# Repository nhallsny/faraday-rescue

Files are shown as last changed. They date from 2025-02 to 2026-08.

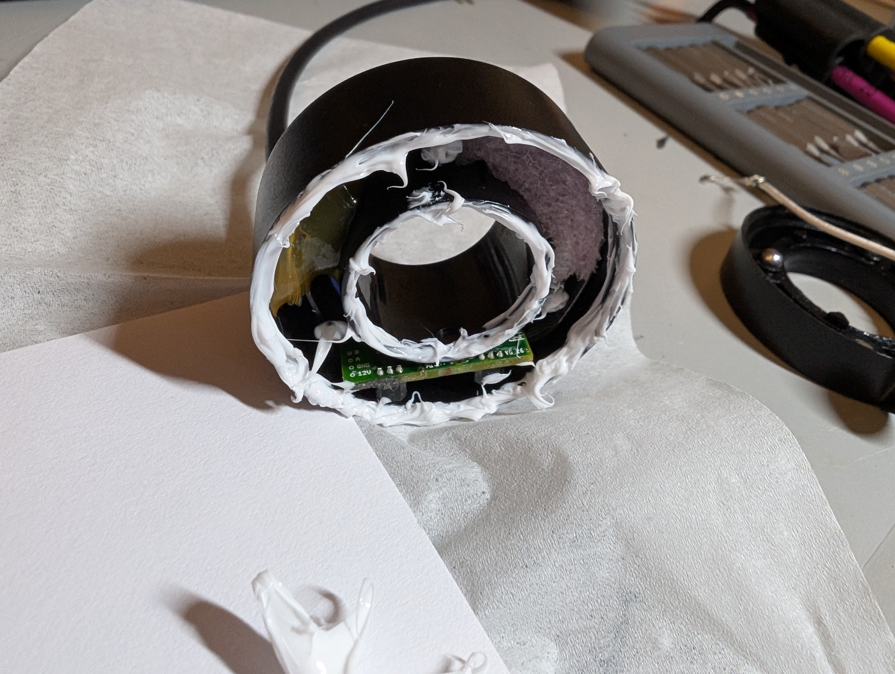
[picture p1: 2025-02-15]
reference/teardowns/mode_selector/PXL_20250124_061346121 - Copy.jpg

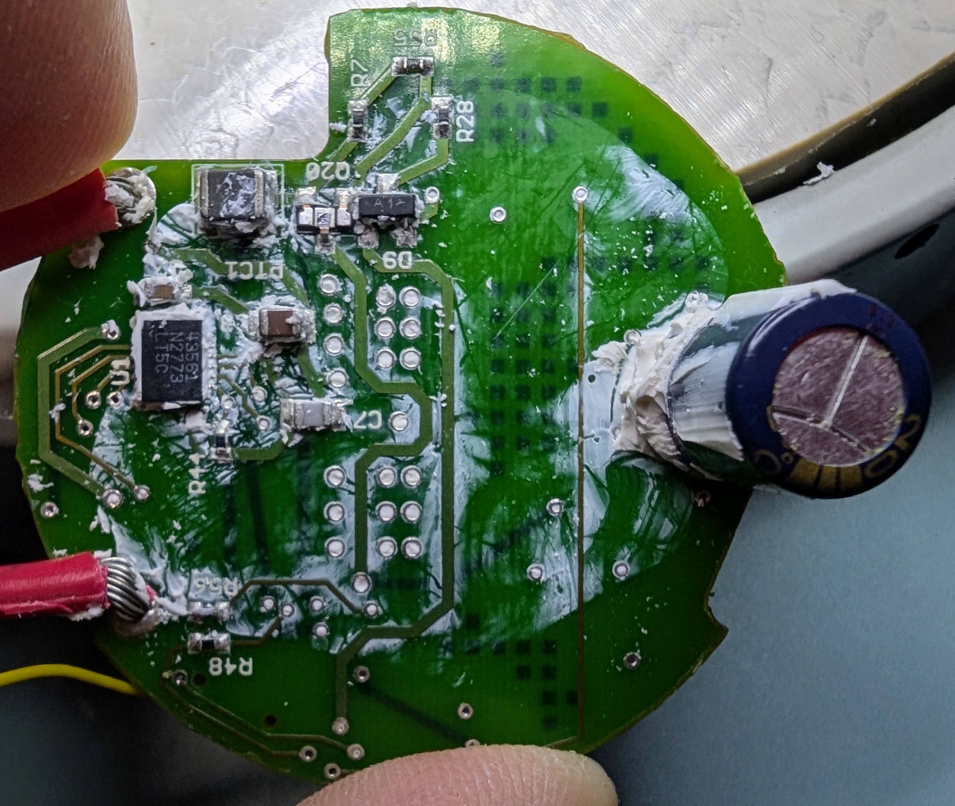
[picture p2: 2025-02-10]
reference/teardowns/bms/PXL_20240805_044113236 (1).jpg

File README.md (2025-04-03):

# faraday-rescue
Open source battery for e-bikes made by the now-defunct Faraday Bicycles

This respository contains designs for an e-bike battery which replaces the original battery in Faraday e-bikes (utilizing exactly nothing from the original battery design!). This design fixes the major flaw in the original design, a high quiescent current which would quickly brick batteries if left un-tended.

## Repository

[build](https://github.com/nhallsny/faraday-rescue/tree/main/build) - CAD/Gerbers

- [cad](https://github.com/nhallsny/faraday-rescue/tree/main/build/cad) - files for printing, lasering, etc
	
- [pcb](https://github.com/nhallsny/faraday-rescue/tree/main/build/pcb) - Gerbers and Kicad project
	
- [build guide](https://github.com/nhallsny/faraday-rescue/tree/main/build/README.md) - Build Instructions
 
[reference](https://github.com/nhallsny/faraday-rescue/tree/main/reference) - design docs, build instructions, original documentation

- [design reference](https://github.com/nhallsny/faraday-rescue/tree/main/reference/design/README.md) - Design Doc
	
- [official](https://github.com/nhallsny/faraday-rescue/tree/main/reference/official) - Original docs and software tools from Faraday
	
- [rebuild](https://github.com/nhallsny/faraday-rescue/tree/main/reference/rebuild) - Instructions to only replace cells
 
[software](https://github.com/nhallsny/faraday-rescue/tree/main/software) - Code
- [bms software](https://github.com/nhallsny/faraday-rescue/tree/main/main/software/bms) - microcontroller code

[test](https://github.com/nhallsny/faraday-rescue/tree/main/test) - How to verify BMS function
- [realtime](https://github.com/nhallsny/faraday-rescue/tree/main/main/test/realtime) - datalogging templates and results

My revived Faraday:


## Battery Redesign Overview
overview


Like the original design, this battery is a 12S 2P 18650 based design. It utilize a PCB the length of the battery for both 'high current' (10A) bussing and for the major BMS controls. Given that the original batteries were designed in 2013, batteries made with modern (2025 as of writing this) have roughly 20% more energy, boosting the range of the bike. However, that's not why this project exists...the project exists because of the many sad Faraday bikes and their unhappy owners. 

Why are their bikes sad? The original battery design has a quiescent draw of around 10mW even when 'off'. While it might not sound like much, that tiny amount of power will drain batteries from 0% state of charge to "bricked" i.e. copper dendrite formation in 2-3 weeks. Left unplugged over the winter, or even a long vacation, the batteries would be irreperably harmed.

How does this battery fix the sleep problem? Modern technology! When the bike was designed, there were no quiescent-optimized battery monitoring chips on the market that could measure 12 cells. The original designer chose an LTC6802-G...a good choice at the time, but designed for electric vehicle batteries with oodles of amp-hours. It doesn't help that the microcontroller on the BMS never seems to sleep. By using a low-power processor, sleep states, and a TI BQ 16-cell BMS chip, I was able to achieve:
+ Original design, off: 300uA
+ This design, off: 3uA

This means that when off, the improved battery can be left at 0% state-of-charge for roughly 5 years before it's a useless hunk of lithium, copper, and cobalt!

### Hardware
+ 12S 2P divided into 8 'modules'
+ Titanium or Fiberglass tube (you choose!)
+ TI BQ76972 fully integrated battery monitoring chip
+ STM32L0 Low-power microprocessor

+ RS485 driver

_Detailed hardware build files are in the [build]([url](https://github.com/nhallsny/faraday-rescue/tree/main/build)) folder

### Software
+ BQ chip implements overvoltage, undervoltage, balancing, temp measurement, high-side FET control, all the super important stuff
+ STM32 manages communications (required!) with the rest of the bike over RS485 and sleep/wake states
+ Currently implemented in C using the STM32 HAL

_Software, debug tools, etc are in the [software](https://github.com/nhallsny/faraday-rescue/tree/main/softwareac) folder_

LICENSE

README.md

## Build instructions
[Build instructions & BOM](https://github.com/nhallsny/faraday-rescue/tree/main/build/README.md)
[JLCPCB BOM](https://github.com/nhallsny/faraday-rescue/blob/main/build/pcb/faraday-rescue-bms/jlcpcb/production_files/BOM-pcb_battery.csv)
Test instructions --> TODO

## Goals

Beautiful, complex objects of the 21st century require 21st techniques to keep them running. Car restoration has been around as long as there have cars, bicycles are no different. However, unlike classic bicycles, e-bikes tend to become e-waste at the first sign of trouble, especially if the company isn't around to provide parts or documentation. In putting this info out there, I hope:
+ Bicycle companies will consider putting documentation for designs online before shutting off part supply forever
+ Motivated enthusiasts (like myself) will consider taking the plunge to keep machines they value alive for another few years.

## Team

+ Project initiator: Nathan Hall-Snyder @nhallsny
+ Contributors:
	+ _[transistor-man](https://github.com/transistor-man) [check out his build log here!](https://transistor-man.com/faraday_bike_revival.html)_

## License

This project is released under CERN Open Hardware Licence Version 2 - Permissive
You can modify and reuse as you like.

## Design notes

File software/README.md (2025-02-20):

# bms

Contains the firmware for the battery management system

# bus-snooper

Python script which converts binary data from a RS485 dump into messages.

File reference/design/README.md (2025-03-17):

# faraday-rescue/reference/design - Design Doc

## Philosophy

Much of this effort was born out of the rather nerve-wracking and labor intensive process of attempting to replace cells on a borked battery pack. The original design required a lot of freehand welding, easy to pinch wires, and opportunities for shorting. The original battery protection system also had high quiescent draw which rapidly bricked the pack if left un-tended. In re-doing the design, the goals were:
- Simplify module welding and bussing
- Achieve a quiescent draw in the low uA range to allow for multi-year storage. This was achieved with a sleep power of around 480uW normally and <50uW in undervoltage lockout.
- Learn embedded software and the modern (as of 2025, anyways) options for hobby electronics projects.

In the PCB design, the goals were:
- Move all critical functions (overvoltage, undervoltage, overcurrent, balancing) to a validated, standard IC
- Use the reference design as much as possible to avoid nasty hardware bugs
- Keep it simple - for example, using a linear regulator and ultra low power processor rather than a more efficient switching regulator

In the software design, the goals were:
- No critical decision making, delgate all important functions to the Battery Management IC
- Reset at every use (avoid bugs from long-term operation).
- Faraday power button must cause a reset
- When in doubt, reset

## String and module design

The original Faraday design featured two module groups - 8x 2P side-by-side groups and 4x 2P end-to-end modules. This arragement results in an intricate series of specialized nickel strips to build the voltage.

This diagram shows the original (top) vs this design (bottom) cell layout.



All of the series/parallel wiring takes place inside the PCB. The routing is rather complex but fortunately, complexity is free on a PCB. The PCB has wide traces (generally at least 10mm and 2 oz copper for a maximum T_rise of around 10C.


Each individual module is identical with the voltage building as shown.


## Cell Selection

I chose a Samsung 35E 18650 for energy density and capability to meet a 10A continuous discharge (in the 2P config).

|Parameter|Limit|
|---|-----|
|Safety Under Voltage - Permanent Fail Subsystem| 1900mV|
|Shutdown Under Voltage| 2400mV|
|Cell Under Voltage| 2631mV|
|Cell Over Voltage| 4199mV|
|Safety Over Voltage - Permanent Fail Subsystem| 4500mV|
|Max Continuous Discharge Current| 8A |
|Min Charge Temperature| 0C|
|Max Charge Temperature| 45C |
|Min Discharge Temperature| -10 C|
|Max Discharge Temperature| 60 C|

I generally added 5C of margin to these in the conservative direction to account for temperature sense inaccuracy.

## Battery ProtectionIC Selection

I chose a BQ76972 for this project for these reasons:
- 16 cell capability
- Integrated linear regulator
- Integrated balancing
- Integrated temperature measurement
- Integrated overcurrent
- Wake function on charger connection
- High side Back to Back FET driver (to match original Faraday design).
- Very small quiescent power in sleep

The original design used an LT6802-G, which was a fine choice at the time but pushed many more critical functions to the processor. Thus, the processor code must be much more thoroughly validated and tested.

## Processor Selection

I chose a STM32L0 for this project for these reasons:
- Low sleep power (<1uA!!)
- Flexible wake inputs (need to wake with a button pull-down to match original faraday design)
- Standard complement of functions (UART, SPI, I2C)
- Independent watchdog
- Real time clock (though I didn't end up using it)
- Available on JLCPCB

## RS485 Driver Selection
This was a real challenge. There are surprisingly few RS485 drivers that meet these criteria:
- Low sleep power (<1uA)
- 3.3V I/O inputs
- Available on JLCPCB

The original Faraday uses a 3.3V RS485 bus so a 3.3V part, while a little non-standard, works fine.

## Power supplies

# Linear regulator

The STM32 and RS485 driver are powered off of REG1 from the BQ76972. REG1 has a recommended current of 30mA and an minimum of 47mA at 0V. Fortunately, the STM32 uses a maximum of 6mA. The power budget is:

|Function|Power|
|---|-----|
|STM32L0 | 6mA |
|RS485 Driver | Vcc/2 / 120 Ohms = 13mA |
|Debug LEDs | 1mA * 4 |
| | Total = 23mA|

REG1 dips a few hundred mV during heavy transmit periods, especially when using the implemented printf funtion for debugging.

At the maximum power draw (30mA), the linear regulator efficincy is laughable (1.3W!), but as long as the BJT used is well coupled to the PCB the deltaT is managable. In normal operation, the LEDs are unused and the RS485 driver is used intermittently.

_Note - the linear regulator is quite sensitive to leakage currents from skin. Touching the caps may interrupt the supply to the BQ chip, resetting the STM32._



## Charge pump

The charge pump takes in battery voltage and boosts it up 10V to provide a high-side drive for the back to back NFETs. This circuit is almost entirely based on the BS76972 reference schematic.


## Sleep/Wake

The design must allow the bike to be woken up in two ways
1. User presses wake button at rear of bike
2. User connects charge cable

To achieve button wake (1), the STM32 uses STOP mode and configures the button active-low as a wake interrupt. Upon waking, the STM32 resets, wakes up the BQ chip, configures it, checks for any error codes, then allows the BQ chip to turn on the back-to-back FETs if allowed.

To achieve charge cable wake (2), the BQ chip is placed into DEEPSLEEP. If a charger is connected (logic level voltage on CD pin), the BQ chip exists DEEPSLEEP and switches to NORMAL. The ALERT output from the BQ chip is configured to only go high when an ADC measurement is ready - this pin goes high a few 10s of milliseconds after the chip boots and is used as a wake interrupt for the STM32.

The corrolary of wake is sleep. The STM32, after a few minutes of inactivity or a user requests the off state, configures the BQ chip for DEEPSLEEP, sets the appropriate interrupts, then enters STOP mode. STOP mode is used because the other STM32 power modes do not support active-low wake interrupts.

The RS485 chip is put into sleep mode by setting RE high and DE low.



A snipped from the schematic


## Fusing

In any battery system, fusing needs a bit of thought. The BQ chip provides a variety of current/time thresholds. I selected a slow-blow ceramic fuse and allow the BQ chip to handle various types of shorts.

Normal events include:
- 9A continuous current from the motor controller
- 60A, ~150us pulse during the turn-on transient

Everything else is abnormal. Ideally, most overcurrents are resettable. Indeed, the BQ chip has a mechanism to handle latching and non-latching short circuit events and return to normal operations.

The fuse coordination chart is shown below:


## PCB Design

The PCB design is extremely constrained by the 41mm diameter tube the batteries must fit into. As such, it must be thin and long



The connectors, test points, fuse, etc must all fit within the narrow arc on top of the cells.



There are three board-mount thermistors which touch the cells with a bit of thermal gap pad.



The board has three connectors:
- XT30 for the main battery connection
- 4 pin Molex Picoblade for the comms connector
- 5 pin Molex Picoblade for the programming connector



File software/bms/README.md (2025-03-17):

# bms software

Contains the firmware for the battery management system as a STM32CubeIDE project using the HAL.

The majority of the software reference material is located in the [design doc](https://github.com/nhallsny/faraday-rescue/blob/main/reference/design/README.md)

## Binaries

[STM32L010K8 .bin File](https://github.com/nhallsny/faraday-rescue/blob/main/software/bms/Release/faraday_stm32_bms.bin)

The .bin file _faraday_stm32_bms_ is compiled for the STM32L010K8 processor. The default build is:
- DEBUG off (not for production, turning this on enables printf and spews lots of debug info over RS485 at 115220 baud)
- LEDs off (not for production, LEDs consume relatively large amounts of power)
- Watchdog On
- Reset 3v3 (not for production, used if the STM32 needs to be hard reset to clear registers related to sleep/wake, such as can happen after debugging).

If you need to change the settings, it's best to get the project running so you can use live debugging.

## Functionality

| Function  |  Responsible | Why?  | 
|---|---|---|
| Overvoltage |  BQ76972 configured by STM32 |  Prevent cells from overcharge |
| Undervoltage  | BQ76972 configured by STM32  |  Prevent cells from undercharge |
| Charging Overtemp Lockout  | BQ76972 configured by STM32  |  prevent cells from charging beyond their rated temperature  |
| Charging Undertemp Lockout  | BQ76972 configured by STM32  | prevent cells from charging below their rated tempertaure  |
| Discharging Overtemp Lockout  | BQ76972 configured by STM32  | prevent cells from discharging above their rated temperature  |
| Discharging Undertemp Lockout  | BQ76972 configured by STM32  |  prevent cells from discharging below their rated temperature |
| Deep Discharge Lockout  | BQ76972 configured by STM32  | prevent deeply discharge and possibly damaged cells from being charged  |
| Overcurrent  | BQ76972 configured by STM32  | turn off immediately when a short circuit occurs  |
| Overcurrent Backup  | 25A, 75V Fuse  | prevent shorting batteries if software and BQ chip fail somehow  |
| Balancing in CHARGE and RELAX | BQ76972 configured by STM32 | Keep cells with a few mV of each other|
| DEEPSLEEP sleep state | BQ76972 and STM32 | Minimize power consumption while off. BQ goes into DEEPSLEEP, STM32 goes into STOP modes|
| SHUTDOWN sleep state | BQ76972 | Dramatically reduce power consumption between 0% SOC and bricking voltage to extend life|
| Wake on insertion of charge plug | BQ76972 and STM32 | Mirror original faraday behavior|
| Wake on momentary pull-down of button | BQ76972 and STM32 | Mirror original faraday behavior |
| Watchdog | STM32 | reset STM32 if code crashes|
| Battery OK message | STM32 | Responds to messages from rear controller to enable high torque mode and update screen|
| Battery voltage message | STM32 | Responds to messages from rear controller to enable high torque mode and update screen|
| Battery balancing message | STM32 | Responds to messages from PC debug tool|
| Debug Compilation Flag | STM32 | Dump lots and lots of info over serial to facilitiate debugging|
| CHG and DSG LEDs | STM32 | Indicate status of FETs|

## Debug with Faraday BMS Tester
[Download Faraday BMS Tester for Windows]([url](https://github.com/nhallsny/faraday-rescue/tree/main/reference/official/Battery%20Utility))
This simple utility uses an RS485-USB adapter hard-coded to COM3 (yes, you have to go deep in device manager and force COM3) to query battery voltages.

Checkboxes force balancing on the original design. The code does not implement this at the moment.



## Debug with STMStudio

[STMStudio](https://www.st.com/en/development-tools/stm-studio-stm32.html) is a great way to read and plot memory addresses. Connect the programming 5p cable to the battery, load these memory addresses in, turn on the battery, and graph away!

| Value  |  Address | Units  | 
|---|---|---|
|  Current |  0x200003fe | int16 mA  |
| Temp 1  | 0x200003e8  | float  |
| Temp 2  | 0x200003ec  | float  |
| Temp 3  |  0x200003f0 | float  |
| Temp 4 - BQ Chip  | 0x200003f4  | float  |
| Min Cell | 0x200003e4  | uint16 mV  |
| Max Cell | 0x200003e6 | uint16 mV  |



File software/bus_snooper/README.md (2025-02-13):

# faraday-rescue/software/bus_snooper RS485 Bus Overview

## Background

The Faraday bike implements the ASI Modbus protocol: https://support.accelerated-systems.com/wp-content/uploads/2022/06/ASI-Modbus-Protocol-Rev-1.2.pdf

## Serial Config

The Faraday uses an half duplex RS485 bus with a minimum signaling voltage of 3.3V. 

RS485 Bus Configuration
Baud: 115200 8/N/1 
Mixed endianness - data is Big, CRC is little

End of message is a RS232 BREAK, which pyserial can’t parse. Need to infer the end of the packet with timing or using a UART device which supports BREAK

## Message Format

Byte 0 is the slave ID. Byte 1 is the function code (0x03 for read, 0x10 for write). The slave responds with the same byte 0 and byte 1 within a few milliseconds of receiving the request.

### Read Register


### Write Register


### Nodes
There are two IDs on the network that respond to requests:
- ID 0x02 - BMS
- ID 0x03 - Mode Selector

Presumably 0x01 is the rear board controller. The ASI motor controller is on a separate bus and communicates directly with the rear board controller.

## Snooping the bus

I was able to parse RS485 messages by using a RS485 USB Dongle, writing all the bus traffic to a text file, and then parsing it after the fact with a script.

`python parse_raw_log.py example.log -v`

***Note: because the RS485 bus uses a BREAK character to signify an end-of-message, which is not supported by PySerial, I wasn't able to parse messages in real time. It's obviously possible with other serial libraries, that work just hasn't been completed.***

# Messages

## Battery Messages

### Cell Voltage Request
Occurs continuously when charging and periodically when biking. Basically a raw output of the LTC AFE used by the battery.

Example:
req 0x02, 0x03, 0x00, 0x02, 0x00, 0x0C, 0xE4, 0x3C

resp 0x2 0x3 0x18 0xa 0x6a 0xa 0x6a 0xa 0x6a 0xa 0x6a 0xa 0x6a 0xa 0x6a 0xa 0x6a 0xa 0x6a 0xa 0x6a 0xa 0x61 0xa 0x60 0xa 0x62 0x87 0xd6

Occurs: when charging, biking, or with battery debug tool
Request:
|SlaveID |FxnCode | Address |Data |Cksum|
|---|---|---|---|-----|
|2|3|0x02|0x0C|Cksum|

Response:

|SlaveID |Register | Length  |Data |Cksum|
|---|---|---|---|-----|
|2|3|24|12x UINT16 * 1.5mV|Cksum|

### Balancing Status Request

Used by debug tool to asking if any of the cells are balancing

Example:

req 0x02, 0x03, 0x00, 0x17, 0x00, 0x01, 0x34, 0x3d

resp TBD
Occurs: with battery debug tool

Request:
|SlaveID |FxnCode | Address |Data |Cksum|
|---|---|---|---|-----|
|2|3|0x17|0x01|Cksum|

Response:

|SlaveID |Register | Length  |Data |Cksum|
|---|---|---|---|-----|
|2|3|2|First 4 bytes are 0. Remaining 12 bits a bitfield. 1 if cell is balancing, 0 if not|Cksum|

### Battery Status 1

Likely a ‘are you there? message’ Occurs continuously while battery is off but rear controller is powered by charger. Response doesn’t seem to change based on mode.

Example:

req 0x2 0x3 0x0 0x0 0x0 0x1 0x84 0x39

resp 0x2 0x3 0x2 0x0 0x0 0xfc 0x44

Request:
|SlaveID |FxnCode | Address |Data |Cksum|
|---|---|---|---|-----|
|0x02|0x03|0x00|0x01|Cksum|

Response:

|SlaveID |Register | Length  |Data |Cksum|
|---|---|---|---|-----|
|0x02|0x03|1|0x00|Cksum|

### Battery Status 2

Purpose unclear. Generally comes after battery read 1. 
Maybe be a temperature or perhaps charge rate? Changes occasionally.

Example:

req 0x2 0x3 0x0 0x1 0x0 0x1 0xd5 0xf9

resp 1 0x2 0x3 0x2 0x8e 0xc4 0x98 0x77

resp 2 0x2 0x3 0x2 0x0 0x19 0x3d 0x8e

resp 3 0x2 0x3 0x2 0x0 0x1e 0x7c 0x4c

Request:
|SlaveID |FxnCode | Address |Data |Cksum|
|---|---|---|---|-----|
|0x02|0x03|0x01|0x01|Cksum|

Response:

|SlaveID |Register | Length  |Data |Cksum|
|---|---|---|---|-----|
|0x02|0x03|2|2 bytes|Cksum|

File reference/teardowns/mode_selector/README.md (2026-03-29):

# faraday-rescue/reference/teardowns/mode_selector

## Known Issues
- Burn-in on the e-paper display
- Water ingress: stress cracking on the plastic housing allows moisture into the pc
- M5 Connector failure: connectors can go high resistance or have water ingress

## Bike Behaviors
- If the mode selector is disconnected or comms messages are not received, the bike will default to 'low' boost.

## Teardown Notes

The mode selectoris a small PCB mounted on the handlebars of the bike which has two functions:
- Select whether the bike is in no boost/medium boost/high boost
- Display the battery SOC% on the e-paper screen

The mode selector has 4 pins:
- GND
- 12V
- RS485 A
- RS485 B

The ePaper display doesn't have a great lifetime and is subject to burn-in. Fortunately, it's pretty simple to replace with a bit of careful prying.

The mode selector is 'waterproofed' with VHB tape. Prying gently at it after removing the screws will expose the innards.
Replacing the VHB is hard without cutting the VHB into the right shape - I used DOW 738 sealant when I put it back together.

The plastic used on the selector is typically cracked by tension from the bolt. I used some acetone to solvent weld it back together.

## Key Parts
MCU: N51822-QFAA
Transciever: MAX3060E
ePaper Display: SCD722003

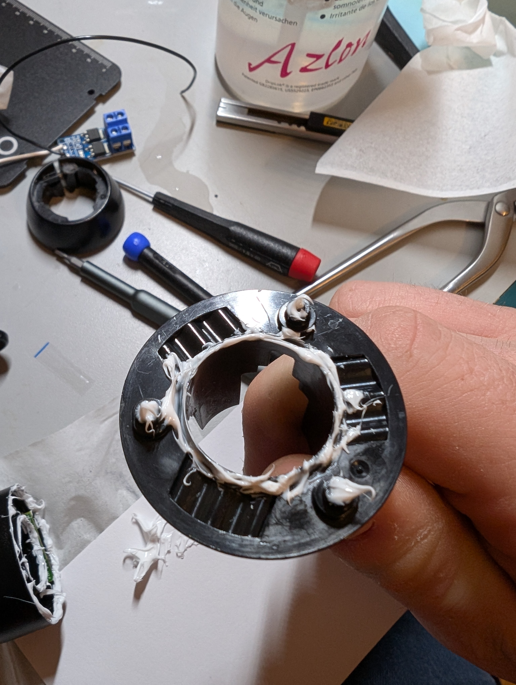
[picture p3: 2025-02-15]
reference/teardowns/mode_selector/PXL_20250124_061343496 - Copy.jpg

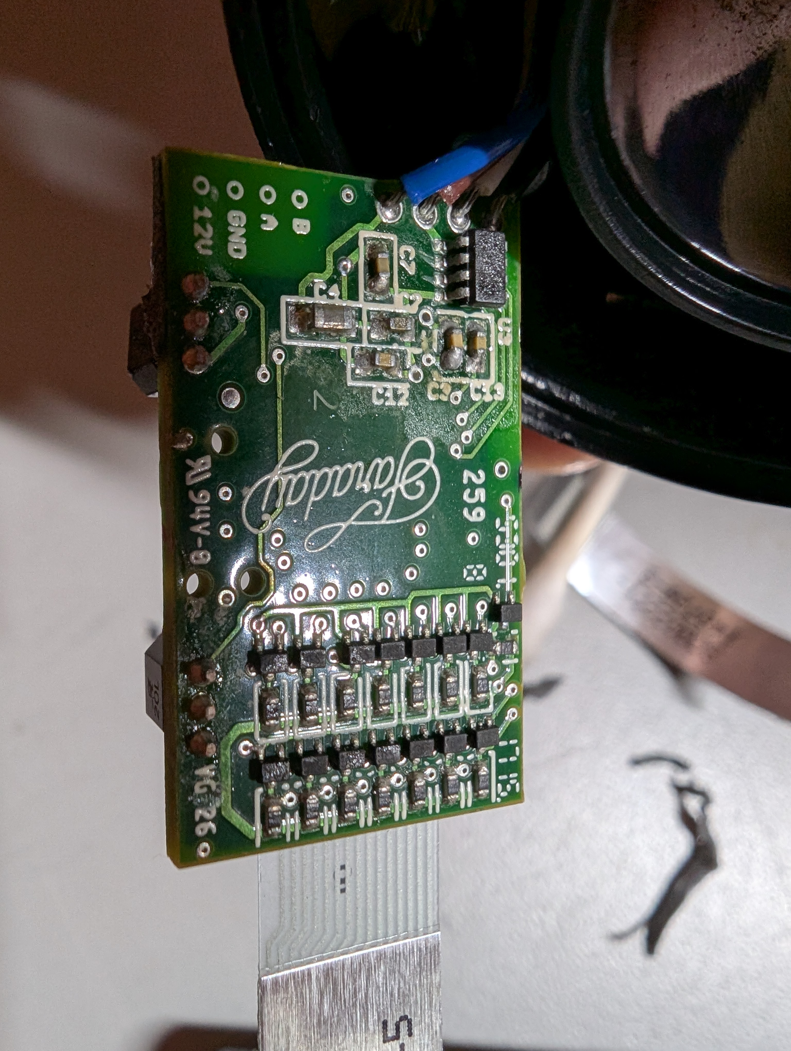
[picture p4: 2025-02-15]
reference/teardowns/mode_selector/PXL_20250124_060525906 - Copy.jpg

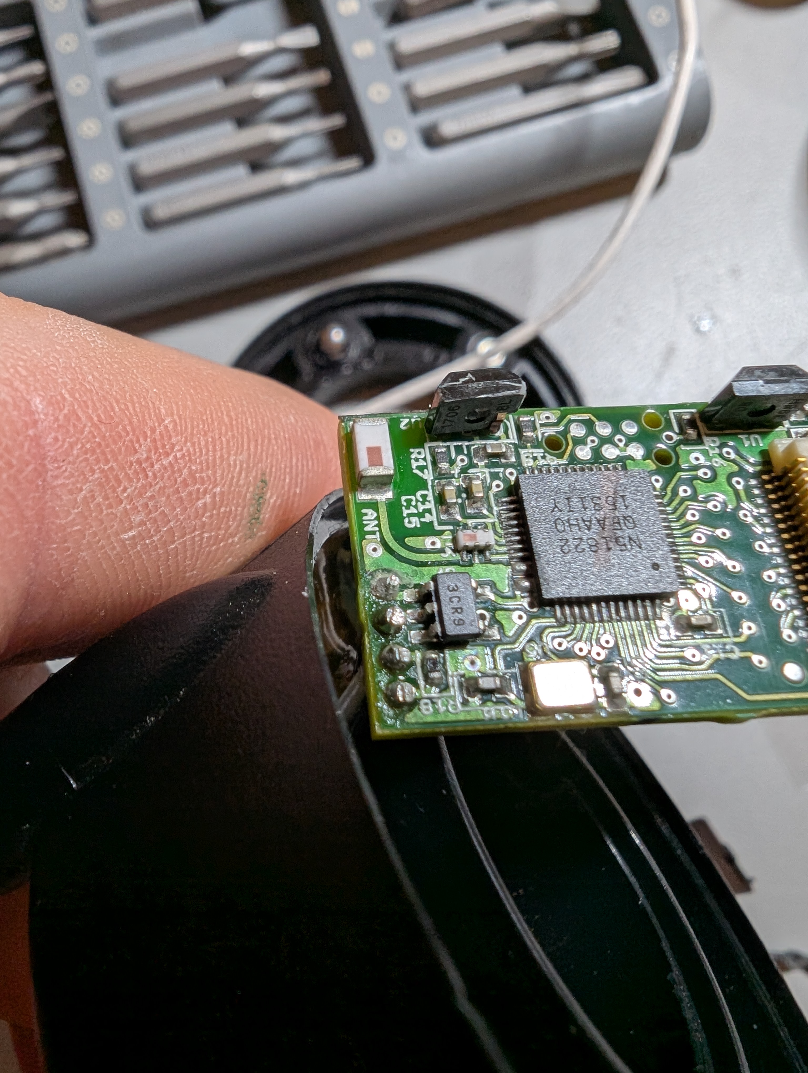
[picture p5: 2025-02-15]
reference/teardowns/mode_selector/PXL_20250124_060510559 - Copy.jpg

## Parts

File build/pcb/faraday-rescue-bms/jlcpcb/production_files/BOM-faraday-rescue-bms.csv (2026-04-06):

Comment | Designator | Footprint | LCSC
100pF 100V | C18 | C_0805_2012Metric | C107105
47nF 100V | C25 | C_0805_2012Metric | C107126
100nF | C13,C24 | C_0603_1608Metric | C113803
1k | R32 | R_0402_1005Metric | C11702
LED | D10,D11,D15,D17 | LED_0402_1005Metric | C123072
2.2uF | C23 | C_0402_1005Metric | C12530
1u 100V | C17 | C_0805_2012Metric | C126585
ABS07-32.768KHZ-T | Y1 | R_1206_3216Metric | C130253
0.47uF 50V | C19 | C_0805_2012Metric | C13967
FCX495TA | Q1 | SOT-89-3 | C150457
100nF | C1,C26,C29,C31,C32,C34 | C_0402_1005Metric | C1525
22nF | C39 | C_0402_1005Metric | C1532
100pF | C20,C21,C28 | C_0402_1005Metric | C1546
10u | C22,C30,C33,C37 | C_0402_1005Metric | C15525
15pF | C35,C36 | C_0402_1005Metric | C1548
0 | R1 | R_0402_1005Metric | C17168
532610571 | J1 | CONN_532610001-SD_05_MOL | C17256390
120 | R19 | R_1206_3216Metric | C17909
PMEG10010ELR | D18,D2,D9 | Nexperia_CFP3_SOD-123W | C179426
20 | R10,R11,R12,R13,R14,R2,R3,R4,R5,R6,R7,R8,R9 | R_1206_3216Metric | C17955
THVD2410DR | U4 | SOIC-8_3.9x4.9mm_P1.27mm | C1849398
BEL Fuse 0ZCJ0005FF2E 50mA 60VDC | F2 | Fuse_1206_3216Metric | C194141
BQ7697202 | U1 | TQFP48_PFB_TEX | C22466635
330 | R45,R46 | R_0402_1005Metric | C25104
~ | 3v3IN1,3v3OUT1,ALRT1,BATT3,BUT1,SCL1,SDA1,VSS1 | TestPoint_Keystone_5019_Minature | C238131
120 | R15,R16,R22,R41,R43,R44 | R_0402_1005Metric | C25079
1 | R47,R49 | R_0402_1005Metric | C25086
330 | R39 | R_1206_3216Metric | C25374
10k | R17,R18,R23,R30,R35,R48,R50,R55 | R_0402_1005Metric | C25744
220K | R24,R26,R29 | R_0402_1005Metric | C25764
1.5k | R20,R21,R33,R34,R37,R38,R42 | R_0402_1005Metric | C25867
5.1K | R25,R27,R28,R51,R52,R53,R54 | R_0402_1005Metric | C25905
7.5k | R31 | R_0402_1005Metric | C25918
SF-1206HHA3000R-2 | F1 | R_2010_5025Metric | C2762483
Thermistor_US | TH1,TH2,TH4 | R_0402_1005Metric | C2889040
1uF | C40 | C_0805_2012Metric | C385977
BZX585-C16,115 | D5,D6,D7 | D_SOD-523 | C455027
STM32L010K8Tx | U2 | LQFP-32_7x7mm_P0.8mm | C456974
DMTH6002LPS-13 | MOSFET1,MOSFET2 | POWERDI5060-8_K_DIO | C461122
220nF 50V | C10,C11,C12,C14,C16,C2,C3,C4,C5,C6,C7,C8,C9 | C_0402_1005Metric | C5159775
1uF | C27,C41,C42 | C_0402_1005Metric | C52923
BAT54SW | D1,D16 | SOT-323_SC-70 | C77325
1N4448W | D8 | D_SOD-123 | C5805633
532610471 | J3 | CONN_532610001-SD_04_MOL | C696092
SMAJ54CA | D21 | D_SMA | C726801
AQHV12-01LTG-C | D19,D22 | D_SOD-523 | C1974808
APCW3216-221P2T | L2 | L_CommonMode_Wurth_WE-CNSW-1206 | C7497124
2N7002 | Q3 | SOT-23 | C8545
0.010 | R40 | R_2512_6332Metric | C875720
ESD9B3.3ST5G | D12,D13,D20,D4 | D_SOD-923 | C96512
BLM18PG471SN1D | FB1 | L_0603_1608Metric | C97853
battery_pod | BT4 | 3S 18650 Group
battery_pod | BT2 | 3S 18650 Group
battery_pod | BT5 | 3S 18650 Group
battery_pod | BT6 | 3S 18650 Group
battery_pod | BT3 | 3S 18650 Group
battery_pod | BT1 | 3S 18650 Group
battery_pod | BT7 | 3S 18650 Group

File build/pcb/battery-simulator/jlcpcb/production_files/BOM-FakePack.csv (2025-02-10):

Comment | Designator | Footprint | LCSC
10 | R1 | R_Axial_DIN0918_L18.0mm_D9.0mm_P22.86mm_Horizontal
TestPoint | TP28 | TestPoint_Keystone_5010-5014_Multipurpose
TestPoint | TP27 | TestPoint_Keystone_5010-5014_Multipurpose
TestPoint | TP26 | TestPoint_Keystone_5010-5014_Multipurpose
TestPoint | TP25 | TestPoint_Keystone_5010-5014_Multipurpose
TestPoint | TP24 | TestPoint_Keystone_5010-5014_Multipurpose
TestPoint | TP23 | TestPoint_Keystone_5010-5014_Multipurpose
TestPoint | TP22 | TestPoint_Keystone_5010-5014_Multipurpose
TestPoint | TP21 | TestPoint_Keystone_5010-5014_Multipurpose
TestPoint | TP20 | TestPoint_Keystone_5010-5014_Multipurpose
TestPoint | TP19 | TestPoint_Keystone_5010-5014_Multipurpose
TestPoint | TP18 | TestPoint_Keystone_5010-5014_Multipurpose
TestPoint | TP17 | TestPoint_Keystone_5010-5014_Multipurpose
TestPoint | TP16 | TestPoint_Keystone_5010-5014_Multipurpose
TestPoint | TP15 | TestPoint_Keystone_5010-5014_Multipurpose
TestPoint | TP14 | TestPoint_Keystone_5010-5014_Multipurpose
TestPoint | TP13 | TestPoint_Keystone_5010-5014_Multipurpose
TestPoint | TP12 | TestPoint_Keystone_5010-5014_Multipurpose
TestPoint | TP11 | TestPoint_Keystone_5010-5014_Multipurpose
TestPoint | TP10 | TestPoint_Keystone_5010-5014_Multipurpose
TestPoint | TP9 | TestPoint_Keystone_5010-5014_Multipurpose
TestPoint | TP8 | TestPoint_Keystone_5010-5014_Multipurpose
TestPoint | TP7 | TestPoint_Keystone_5010-5014_Multipurpose
TestPoint | TP6 | TestPoint_Keystone_5010-5014_Multipurpose
TestPoint | TP5 | TestPoint_Keystone_5010-5014_Multipurpose
TestPoint | TP4 | TestPoint_Keystone_5010-5014_Multipurpose
TestPoint | TP3 | TestPoint_Keystone_5010-5014_Multipurpose
TestPoint | TP2 | TestPoint_Keystone_5010-5014_Multipurpose
TestPoint | TP1 | TestPoint_Keystone_5010-5014_Multipurpose
0.1 | R13 | R_1206_3216Metric
1 | R26 | R_0805_2012Metric
1 | R25 | R_0805_2012Metric
1 | R24 | R_0805_2012Metric
1 | R23 | R_0805_2012Metric
1 | R22 | R_0805_2012Metric
1 | R21 | R_0805_2012Metric
1 | R20 | R_0805_2012Metric
1 | R19 | R_0805_2012Metric
1 | R18 | R_0805_2012Metric
1 | R17 | R_0805_2012Metric
1 | R16 | R_0805_2012Metric
1 | R15 | R_0805_2012Metric
1 | R14 | R_0805_2012Metric
10 | R12 | R_Axial_DIN0918_L18.0mm_D9.0mm_P22.86mm_Horizontal
10 | R11 | R_Axial_DIN0918_L18.0mm_D9.0mm_P22.86mm_Horizontal
10 | R10 | R_Axial_DIN0918_L18.0mm_D9.0mm_P22.86mm_Horizontal
10 | R9 | R_Axial_DIN0918_L18.0mm_D9.0mm_P22.86mm_Horizontal
10 | R8 | R_Axial_DIN0918_L18.0mm_D9.0mm_P22.86mm_Horizontal
10 | R7 | R_Axial_DIN0918_L18.0mm_D9.0mm_P22.86mm_Horizontal
10 | R6 | R_Axial_DIN0918_L18.0mm_D9.0mm_P22.86mm_Horizontal
10 | R5 | R_Axial_DIN0918_L18.0mm_D9.0mm_P22.86mm_Horizontal
10 | R4 | R_Axial_DIN0918_L18.0mm_D9.0mm_P22.86mm_Horizontal
10 | R3 | R_Axial_DIN0918_L18.0mm_D9.0mm_P22.86mm_Horizontal
10 | R2 | R_Axial_DIN0918_L18.0mm_D9.0mm_P22.86mm_Horizontal
Screw_Terminal_01x13 | J4 | TerminalBlock_Xinya_XY308-2.54-13P_1x13_P2.54mm_Horizontal
Screw_Terminal_01x02 | J3 | TerminalBlock_4Ucon_1x02_P3.50mm_Horizontal

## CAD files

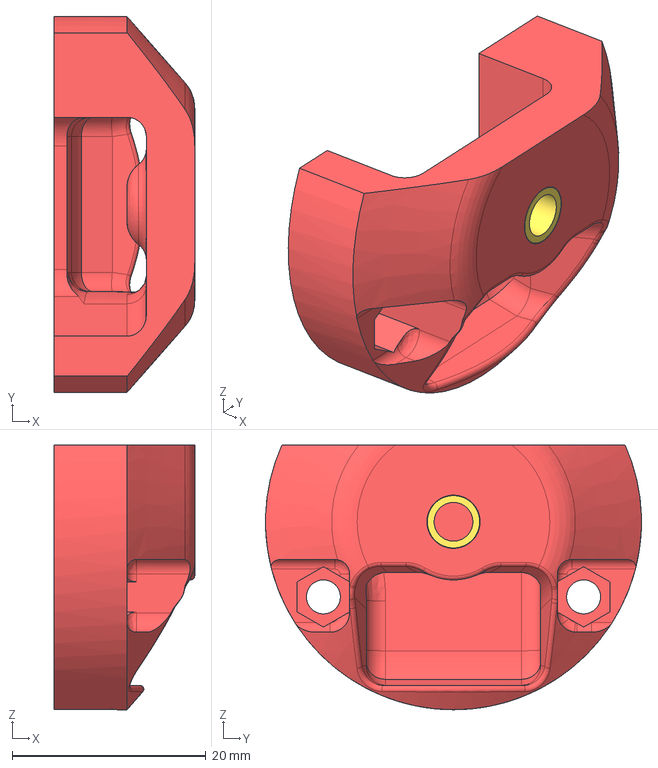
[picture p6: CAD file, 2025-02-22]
build/cad/3dprint/end_bracket_wire_side-v31.step
14.5 x 38.8 x 27.3 mm

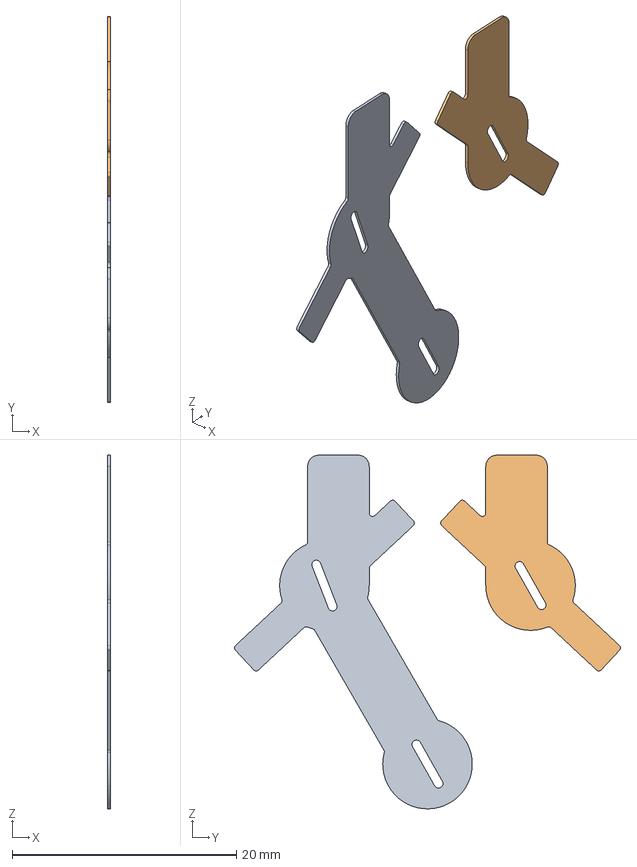
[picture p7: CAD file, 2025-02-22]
build/cad/lasercut/weld_tab_large-v42.step
0.25 x 34.5 x 31.6 mm
Tab 2
Tab 1

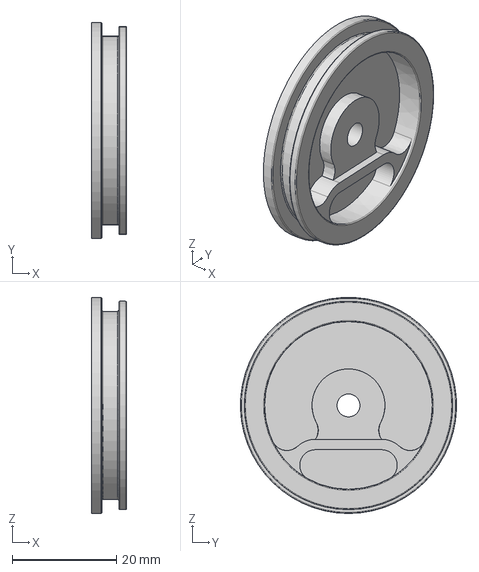
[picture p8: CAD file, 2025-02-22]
build/cad/machining/tube_cap-v14.step
6.75 x 41.5 x 41.5 mm

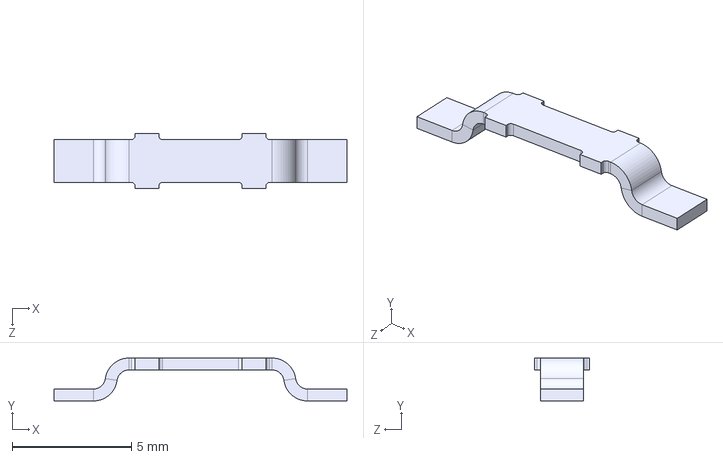
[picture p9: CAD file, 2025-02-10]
build/pcb/faraday-rescue-bms/custom symbols/5104/5104.step
12.3 x 1.80 x 2.30 mm

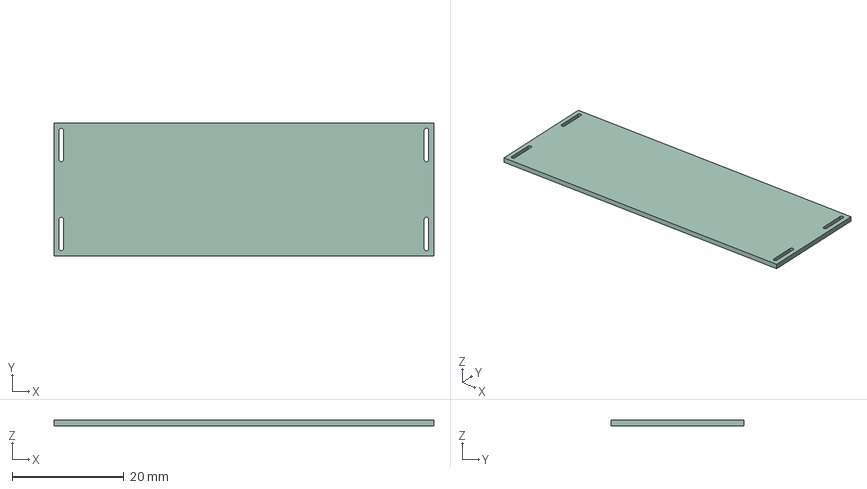
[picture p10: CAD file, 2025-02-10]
build/pcb/faraday-rescue-bms/pcb_battery_stub.step
67.9 x 23.7 x 1.00 mm

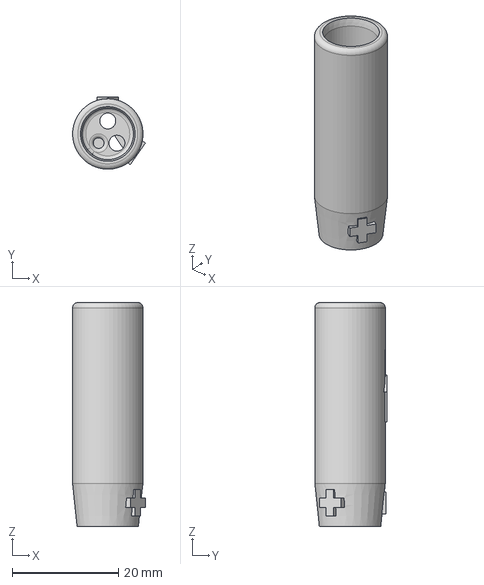
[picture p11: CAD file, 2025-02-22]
build/cad/3dprint/power_connector-v11.step
13.8 x 13.7 x 42.3 mm

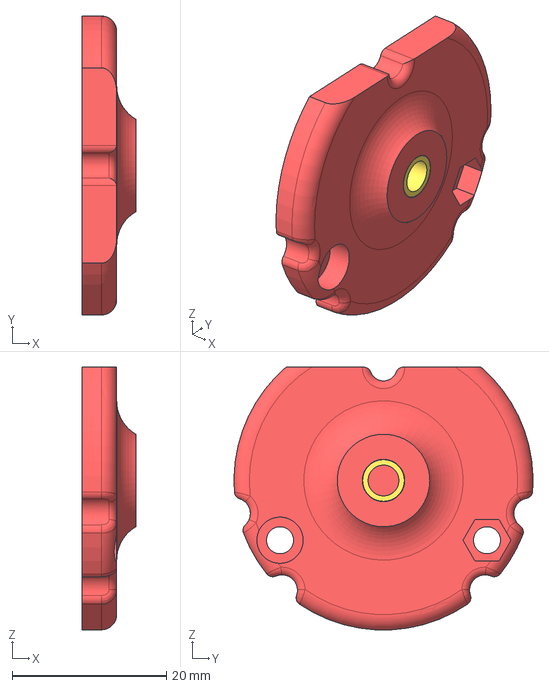
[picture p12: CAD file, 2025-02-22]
build/cad/3dprint/end_bracket_non_wire_side-v10.step
7.00 x 38.8 x 34.1 mm

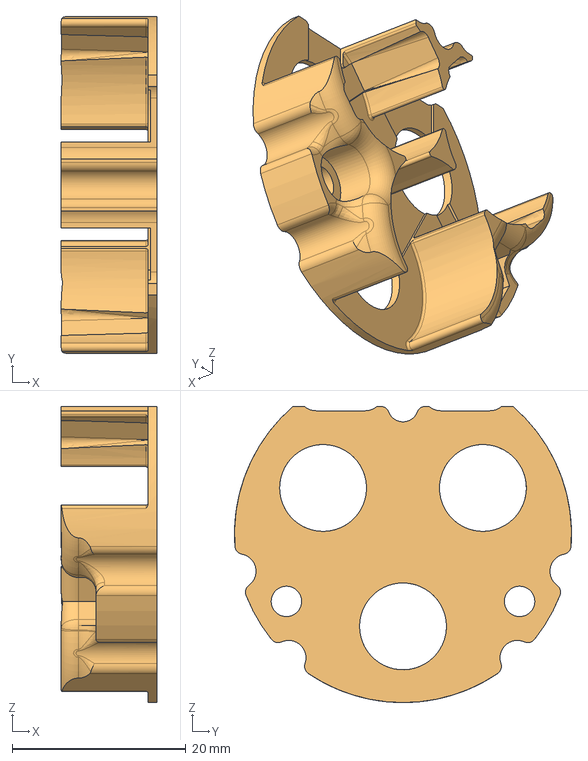
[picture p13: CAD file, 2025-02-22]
build/cad/3dprint/module_end-v41.step
11.0 x 38.8 x 34.1 mm

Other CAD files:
build/cad/lasercut/weld_tab_small-v42.step
build/cad/3dprint/end_bracket_non_wire_side-v10.stl
build/cad/3dprint/end_bracket_wire_side-v31.stl
build/cad/3dprint/module_end-v41.stl
build/cad/3dprint/power_connector-v11.stl
build/cad/lasercut/weld_tab_large-v42.dxf
build/cad/lasercut/weld_tab_small-v42.dxf

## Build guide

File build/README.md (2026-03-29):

# faraday-rescue/build Build Guide

## Intro

This is a build guide for assembling a faraday rescue battery.

## Required Tools
- General small hand tools - hex wrenches, x-acto knife, wire cutters/strippers
- 18650 Spot welder
- Soldering iron with chisel tip
- Solder
- Fine-pitch crimper (for Molex Picoblade)
- Large-pitch crimper (for TE 1.5mm crimps)
- Heat gun
- Isopropanol wipes
- Calipers
- Button Harness (see below)
- STLink to Green Julet Adapter Harness (see below)

## Bill of Materials
| Part Number | Description | Quantity | Link |
|---|---|---|---|
| INR18650-35E | Batteries | 24 | https://www.18650batterystore.com/products/samsung-35e |
| weld_tab_large-v42 | Custom Nickel Tabs, 0.15mm | 16 | Laser or Waterjet Cut |
| weld_tab_small-v42 | Custom Nickel Tabs, 0.15mm | 16 | Laser or Waterjet Cut |
| module_end-v41 | Module end caps | 16 | 3D Print 10% GF ASA |
| end_bracket_wire_end-v31 | Module stack end cap, wire side | 1 | 3D Print 10% GF ASA |
| end_bracket_non_wire_end-v10| Module stack end cap, non-wire side  | 1 | 3D Print 10% GF ASA |
| power_connector_v11 | Battery to faraday power connector  | 1 | 3D Print 10% GF ASA |
| PCB, Long | Custom PCBA | 1 | JLCPCB |
| PCB, Short | Custom PCB | 1 | JLCPCB |
| Thermal paste or 2mm gap pad, cut into 6mm squares | Thermally conductive, insulating heat transfer pad for thermistors | 3 | Amazon |
| tube_cap-v14 | Aluminum tubing end cap | 2 | JLCPCB |
| Keyelco 5104 | Jumpers between PCBs | 4 | Digikey |
| Wire 16ga | Power wire, red/black | 2 | Digikey |
|Molex / 0500798100 |26-28 Awg Picoblade Crimp | 9 | Digikey |
|Molex / 0510210500 |CONN RCPT HSG 5POS 1.25MM |1 | Digikey | 
|Molex / 0510210400 |CONN RCPT HSG 4POS 1.25MM |1 | Digikey |
|TE 929990-1 | CONTACT SOCKET 13-17AWG CRIMP|2 | Digikey |
| (Preferred) 42mmx0.9mm thickness Ti | Tube, 568mm long | 1 | WEN Titanium --> https://www.ebay.com/itm/174293717819  |
| (Backup, Verified) BT60 Fiberglass Tube, Cut to Length | Tube, 568mm long | 1 | [Mach 1 Rocketry](https://www.mach1rocketry.com/product-page/fiberglass-airframe-tubes)  |
| (Backup, Verified) Carbon Fiber, 42mm x 1.0mm thickness, Cut to Length | Tube, 568mm long | 1 | [Ebay or similar](https://www.ebay.ca/itm/132443490003) |
| a21042700ux0068 | Thin Heatshrink PVC, 70mm flat, preferably clear| | 1 | Amazon/Uxcell |
| Pre-wired Julet Connector 200mm | 4 pin (blue) Julet connector, male | 1 | Amazon |
| Pre-wired Julet Connector 200mm | 5 pin (green) Julet connector female | 1 | Amazon |
| 15mm Breather Patches| 15mm self-adhesive Gore stickers | 1 | https://www.dapperlighting.com/products/15mm-breather-patches?variant=49163249484050 |
| 1289N171 | End-cap o-ring | 2 | https://www.mcmaster.com/1289N171/ |
| O-ring lube | O-ring Lubricant, Silicone or other | 1 | Local hardware store |
| 97163A152 | Insert, M4, 5mm long | 2 | https://www.mcmaster.com/97163A152/ |
| Dow 738 | RTV Sealant | 1 | https://www.mcmaster.com/1832A51/ |
| 91292A027 | M3 Bolts | 18 | https://www.mcmaster.com/91292A027/ |
| 93625A100 | M3 Locknuts | 18 | https://www.mcmaster.com/93625A100/ |
| Loctite 4861 or similar medium viscosity glue | CA flexible adhesive | 1 | https://www.mcmaster.com/74795A74/ |
| 5233T358 | Small O-rings | 2 | https://www.mcmaster.com/5233T358/ |
| 90991A121 | End-cap bolts, non-wire side | 1 | https://www.mcmaster.com/90991A121/ |
| 90991A124 | End-cap bolts, wire side | 1 | https://www.mcmaster.com/90991A124/ |
| | | | |

## Build Instructions
You’ll need 8x of these modules:


Pre-assemble 16 end plates by gently placing the tabs and press-fitting the nylon locknut


Place the end-caps onto the batteries with the battery polarity as shown.
_NOTE - ALL CELLS MUST BE IN THE EXACT SAME ORIENTATION IN ALL MODULES_


Weld the modules. I used 6 welds per tab. Welding prior to gluing prevents the glue from wicking between the tabs and cells


Applying gentle force to the top, add 1 drop of thin superglue to the space between the cells. Verify with calipers that the stack height is no greater than 67.8mm



Repeat 8 times.


8 Modules welded, glued, and inspected


Solder the XT30 connector to the bottom of the board, making sure to match + and - to the labels on the board (VOUT)


On a flat surface, solder the 4 Keystone jumpers between the main and stub pcb
_Note - this is only necessary if you can't find a vendor who will make the full length board_


Wrap 1/4" Kapton tape in a loop around the jumpers. Make sure to cover the underside to avoid shorting during soldering.


Add ~1mm thermal gap pad or thermal paste to thermistors on back-side of board. I conformal coated these sensors, probably unnecessarily.


Bolt together, align, and install the first two modules


Place, bolt, and solder the remaining modules. Adjust the modules prior to soldering to eliminate twist and non-concentric modules as much as possible.


Heat-set the insert into the non-wire-side end cap


Bolt the end-cap into place onto the side with the stub PCB (the negative-most side). The bolts should be flush or close to flush.


Test fit the end-cap to make sure it fits flush


Heat-set the M4 insert into the wire-side end cap and install 2 nuts.
_Note - having two nuts on this side technically violates the bolt/nut pattern, but trust me, it's way easier to assemble this way._


Measure your wire sizes and drill 5 holes into the end cap based on the wire sizes. Take care to make sure there are no wire crosses once installed. The 5th hole is for the breather vent.



_Note - the wires must be lined up in order to avoid crosses. There isn't much space in the end_



Wipe the surface with isopropanol, let dry, and the adhere the the vent to the outside



Pre-crimp the four wires 
- Positive Power (crimp bike end with TE female crimp)
- Negative Power (crimp bike end with TE female crimp)
- RS-485 (Light Blue 4-pin Julet Connector, Male, with Picoblade crimps)
  
  
  
  

- SWD Programming Header (Green 5-Pin Julet Connector, Female, with picoblade crimps)
- 
- 
- 




Apply a bit of thick tape (I used fiberglass tape) to prevent the thin wires from getting cut by the battery tab


Insert the power wires into the printed housing


Pass the power wires through the holes drilled (no picture)

Solder the XT30 to the backside



Pot the back of the housing with DOW 738 (in green). Use a toothpick to make sure that the coverage is 100%


Wait for the DOW 738 to dry

Flash the .hex file onto the STM32 and test your new battery! If you have flashed with LEDS = 1, then the CHG and DSG lights should light up. If not, try shorting BUTTON and GND. TODO image
_Note - the LEDs consume significant power and cause heating of the linear reg. I suggest flashing with LEDS = 0 after debugging_
_Note 2 - I made a 'faraday on/off' harness with RS485 and the on/off button broken out. See 'tools' section below_



When satisfied, heat-shrink the battery. This takes a bit of practice to get a consistent diameter (no wrinkles allowed to fit in a 40mm tube), make sure you have extra heatshrink to try a few times. I heated the cells first to remove wrinkles, then tensioned the heatshrink by heating the valleys.



Apply a light coat of o-ring lubricant on the o-rings and install o-rings on the aluminum end caps



Install the wire-side cap (if you haven't already). Use the small 4mm ID o-ring to achieve sealing with the M4 bolt. (no picture)

Make sure that the inner diameter of both sides of the tube are deburred and lightly chamfered with sandpaper or a file. Burrs and sharp edges are your enemy. Clean the inside of the tube.

Slide the tube over the entire battery. Some gentle pressure and a light coating of grease may be required. (no picture)

_Note - if too much force is used, the heatshrink may bunch and rip, possibly shorting the battery. Go gently.

Bolt on the remaining end-cap with o-ring and lubriant. Make sure that the o-ring is engaged with the tube.



Final test procedure
| Test |Expected Result | Tool |
|---|---|---|
| Charge | Cut-off around 4.2V | 2A, 51V power supply or Faraday Charger with DIY harness | 
| Discharge | Cut-off around 2.7V | 1-5A discharge through power resistor or programmable load | 
| Verify balance | Almost no imbalance (<0.020V) | Faraday BMS Tester |
| Check temperatures | 4x rational temperatures | STMStudio Direct Memory Address Reader (see software documentation) | 

# Tools

## ST-Link to Green Julet Adapter Harness

Use this adapter to program the processor or read parameters with STMStudio

| Part Number | Description | Quantity | Link |
|---|---|---|---|
| ST-Link V2 | PRogrammer | 1 | Digikey |
| 0901420020 | Molex 20 Pin header adapter | 1 | Digikey |
| 0016020088 | Molex C-Grid Crimps | 1 | Digikey |
| Julet 5-pin Green connector, Male | Crimps | 1 | Digikey |

Note that you will need to double crimp the 3.3V wire to provide a reference voltage for the STLink like so:



## Button Harness

Use this to turn the battery on and off and connect it to RS485
| Part Number | Description | Quantity | Link |
|---|---|---|---|
| Waveshare 17286 | RS485 to USB Converter | 1 | Amazon |
| No Part Number | Julet 4-pin blue connector, female | 1 | Amazon |
| Any momentary switch | Crimps | 1 | Amazon |

Note - COLORS ARE NOT STANDARDIZED ON THESE AMAZON CABLES. Check your pinouts!

PCB Pin 1 - GND----------Red------GND----BUTTON

PCB Pin 2 - BUTTON ------Green----BUTTON

PCB Pin 3 - RS485 A -----Black----RS485 A

PCB Pin 4 - RS485 B -----White----RS485 B





## Sizer Ring
I suggest printing a 40mm sizer ring to pass over the battery prior to heat-shrinking. This verifies that it will go in the tube smoothly.


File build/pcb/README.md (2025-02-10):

# faraday-rescue/build/pcb
Contains KICAD (produced in KiCAD 8.0.4 of the following:
- faraday-rescue-bms - the main thing, the schematic, layout, and manufacturing files for the PCB that turns a bunch of cells into a battery
- battery-simulator - simple PCB with 12 resistors in series for testing BMS functions such as overvoltage, undervoltage, leakage currents, etc

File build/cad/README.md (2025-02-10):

# faraday-rescue/build/cad
Step files of the battery assembly
- faraday-battery-mechanical.step - .STEP file of the entire assembly
- faraday-rescue-bms.step - .STEP file of the PCBA with most of the components present (all the important ones, anyways)

Contact me directly for raw files.

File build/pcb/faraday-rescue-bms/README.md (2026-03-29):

# faraday-rescue/build/pcb/faraday-rescue-bms

PCB attached to battery modules that measures voltages, protects battery, manages sleep/wake, communicates with Faraday bike over RS485

## Revision table
### Release 2.1
- Change RS485 TVS diodes to bidirectional

### Release 2.0	
  - Fixed incorrect diode footprints
  - Fixed C15 Silk
  - Added VSS Test Point
  - Adjust I2C Pullups to 1.5kOhms
  - Add Cell0-VSS GND tie
  - Add more bulk capacitance near STM32 and RS485 Chip
  - Increase capacitance on BUTTON for more debouncing
  - Change shunt for a smaller one
  - Add thermal reliefs for SMT components on ground planes
  - Remove CHG and DSG test points
  - Add easy test points for sleep current measurement
  - Change thermistor capacitance to <470pF
  - Change to larger 20A slow-blow fuse for higher voltage rating
  - Add picoblade connector for RS485/button connector
  - Changing programming header to picoblade

Considered but not implemented:
  - Add bluetooth module for STM32
  - Switch Linear regulator to switching regulator
### 1.0
Initial Release

## Using these files
These files were designed in KiCad 8.0.4. There are two PCBs to fit in JLCPCB's design rules:
- Long, thin pcb which contains the BQ chip, STM32, and connectors
- Small stub board to complete the 8th module.

### Manufacturing parameters
If sending out this PCB, I suggest the following for the main PCB:
- 1mm board thickness (to fit inside tube)
- 2oz copper thickness on all layers (to reduce resistive heating. May not be necessary at 9A max current)
- Higher Tg material to avoid degredation of insulation during operation

For the smaller stub PCB:
- 1mm board thickness
- 1oz copper
- Higher Tg material to avoid degradation of insulation during operation

Ordering parameters from JLCPCB:


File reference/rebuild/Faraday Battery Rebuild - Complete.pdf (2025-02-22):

Warning: Please use extreme caution in handling Li-ion batteries as they can sever electrical and thermal burns if they are improperly handled. These instructions are provided for educational purposes only. Please observe all safety precautions including having a fire extinguisher. A Li-ion battery rebuild is best left to experts.

## Part 1. Faraday Lithium-ion Battery Rebuild

1. Parts List and Tools
Item | Where to Buy | Quantity | Price | Total Price | Comments
Sanyo NCR18650GA 3500mAh 10A Li-ion cells | https://www.18650batterystore.com (https://www.18650batterystore.com/products/sanyo-ncr18650ga?variant=37119893373079) | 24 | @$6.00 for 10+ | $144 | You need 24 cells for the Faraday battery, but it will handy if you have more since you’ll probably mess a few along the way
kWeld – Complete Kit | https://gridrewired.com/ (https://gridrewired.com/en-us/products/kweld-spot-welder-kit) | 1 | $238 | $238 | You will need a spot welder to attach the nickel strips to the battery. After having tried several cheaper ones, I settled on this. It just works on 0.2mm thick nickel strips
TURNIGY GRAPHENE PANTHER 5000MAH 3S 75C BATTERY PACK | Hobbyking.com (https://hobbyking.com/en_us/graphene-5000mah-3s-75c.html) | 1 | $65.97 | $65.97 | This the battery you need to use the kWeld.
LiPo Charger for Lipo Battery | Amazon.com (https://www.amazon.com/gp/product/B07R18YNZQ/ref=ppx_yo_dt_b_search_asin_title?ie=UTF8&psc=1) | 1 | $56 | $56 | Charger for the LiPo battery for kWeld
Li-ion cell charger/tester | SkyRC MC3000 (https://www.18650batterystore.com/products/skyrc-mc3000?variant=37119895634071) or Megacell Charger and Software (https://gridrewired.com/en-us/products/megacell-charger-and-software) | 1 | $99 or $245 | $99 or $245 | It’s a good practice to charge or condition your cells prior to assembling them. I’ve give you 2 options that I think are very good. I bought the SkyRC MC3000 but that’s because I didn’t know of the Megacell option.
60W soldering Iron | Amazon.com (https://www.amazon.com/Soldering-Iron-Kit-Temperature-Rarlight/dp/B07PDK3MX1) | 1 | $10 | $10 | Any one will do but this one is the model I purchased
Sheet metal cutter | Amazon.com (https://www.amazon.com/Metal-Sheet-Cutters-Right-Straight/dp/B0841NLFMS) | 1 | $16 | $16 | Any generic sheet cutter will do. Even a pair of kitchen scissors may suffice but you might have to chuck them since you’ll pretty much destroy the cutting edges
Barley Paper Battery Insulator Rings | Amazon.com (https://www.amazon.com/gp/product/B07H6TF58L/ref=ppx_yo_dt_b_asin_title_o09_s00?ie=UTF8&psc=1) | 1 | $8.88 | $8.88 | Optional but I ended up using them it’s a good way to avoid shorts
Soldering Lead (0.8mm) | Amazon.com (https://www.amazon.com/gp/product/B075WB98FJ/ref=ppx_yo_dt_b_asin_title_o06_s00?ie=UTF8&psc=1) | 1 | $8.98 | $8.98
Battery Welding Holders | Amazon.com (https://www.amazon.com/gp/product/B09DCYWQKN/ref=ppx_yo_dt_b_asin_title_o07_s00?ie=UTF8&psc=1) | 1 | $10.49 | $10.49 | Optional but helpful to keep the cells steady as you weld the nickel strips
100% pure Nickel strips 0.1mm x 6mm 100% pure Nickel strips 0.15mm x 8mm | Amazon.com (https://www.amazon.com/gp/product/B07Y1FDKCP/ref=ppx_yo_dt_b_asin_title_o01_s00?ie=UTF8&th=1) | 1 of each @$21 | $42 | $42
Nickel tabs | Amazon.com (https://www.amazon.com/dp/B07PGSVRCT?psc=1&ref=ppx_yo2ov_dt_b_product_details) | 1 | $6.99 | $6.99 | Optional. You could just fashion these tabs yourself but having these for Part B makes it easier
Thermal Glue | Amazon.com (https://www.amazon.com/gp/product/B072MSXHJD/ref=ppx_yo_dt_b_asin_title_o07_s00?ie=UTF8&psc=1) | 1 | $9.99 | $9.99
Heat resistant tape ½” | Amazon.com (https://www.amazon.com/gp/product/B07K1W8FTW/ref=ppx_yo_dt_b_asin_title_o01_s01?ie=UTF8&psc=1) | 1 | $11.99 | $11.99 | You’ll need this to insulate a set of connectors for Part B of the Battery
Heat shrink tubing 70mm x 2m | Amazon.com (https://www.amazon.com/gp/product/B07VYJCRZ3/ref=ppx_yo_dt_b_asin_title_o06_s00?ie=UTF8&psc=1) | 1 | $5.39 | $5.39 | As a final step, you’ll slide your battery into this tubing and use a strong hair dryer to shrink wrap and protect it.
| | | Total | $625 + $99/$245 plus shipping

## Part 2. Faraday Li-ion Battery Disassembly

In this section, we’re going to disassemble your ebike’s Li-ion battery. And before you can attempt this, you must remove the battery from within the bicycle.

Here’s a link to video by Faraday bikes that shows you how to do this. https://www.faradaybikes.com/support-articles/component-installation-guides/battery-replacement/

Before proceeding, we should take a moment to briefly discuss the overall procedure of rebuilding the battery. The best way of thinking about the next few steps is that you are going to be replacing the cells housed within the battery, much as you might in your TV remote. The only difference is that your TV remote battery compartment is designed for user serviceability, whereas an modern Li-ion battery is more complex and not designed for anyone except experts to service. Another thing to bear in mind is that a Faraday battery was constructed with severe physical constraints in terms of dimensions, size and ruggedness. A bicycle receives lots of shocks and you wouldn’t want your bike to go up in flames when you hit the kerb really hard! As you go about disassembling the battery in this stage and rebuilding it, one really has to take the approach that you’re literally doing the exact same thing as with changing your TV remote batteries. All the battery cells, connectors, wires, placement etc will be replaced as you found it. Don’t make the mistake that I made with my first battery where I thought that I could get away with some sloppiness, thicker wire here or there should be fine, right? No, you cannot as space is at a premium and the Faraday engineers built the battery with the most optimal placement of everything.

If all that isn’t daunting enough, remember that you cannot have any things jutting out or an extra bit of solder poking out. Li-ion batteries are incredibly energy dense and regular insulators are just not sufficient at times. Most of these flaws will manifest as you try to squeeze the cells back into the tube. The good news is that once you’ve rebuilt your Faraday battery, you can pretty much rebuild any Li-ion battery out there!

I recommend that you spend lots of time just observing how the original battery was constructed as you attempt to replicate that exactly. Bear in mind, you have to insert the battery back into the original tube and it won’t fit if you’re not careful. Follow the steps below and hopefully you should be able to have a usable battery that works just like the original one.

Coming back to disassembling the battery, it isn’t particularly hard, but as with attempting anything the first time, it appears to be a bit more complex than it is. But once you’ve retrieved your battery it should look like this. It’s a long cylinder with wires dangling off one end, as shown in the picture below.

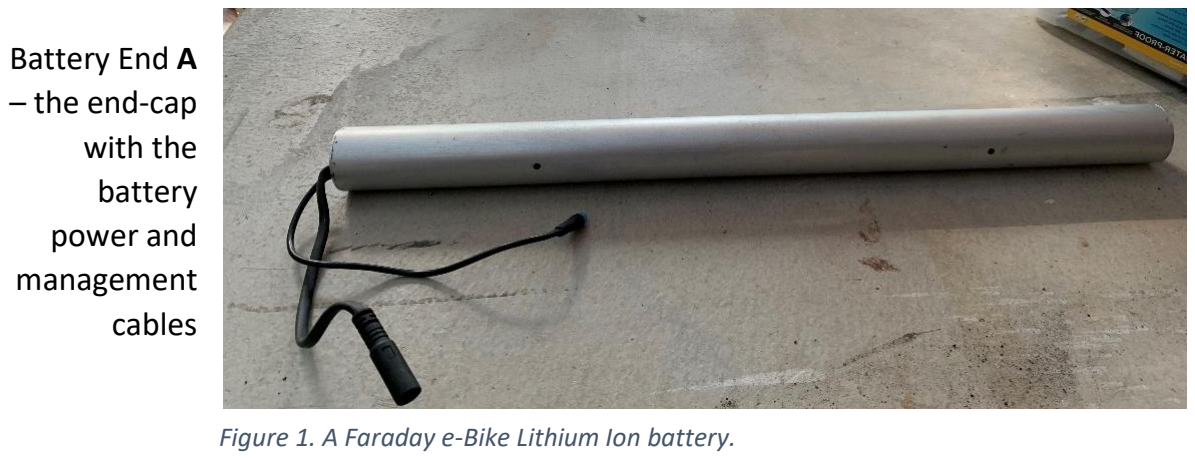
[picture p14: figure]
Battery End A – the end-cap with the battery power and management cables

Figure 3. This picture shows where you place the hacksaw blade to create an edge.

Use a fine-toothed hacksaw to create a groove around the end caps, and then use a flat-head screwdriver to gently pry it apart. There is some silicone adhesive you are trying to overcome, but also the crimping on the end (those little divets) that secure into a circumferential groove on the end-caps. Using a narrow width flat-head screwdriver helps. Be patient as its quite easy to “tear” the aluminium as you pry with a screwdriver. You want to preserve the shape as much as possible and not introduce any sharp edges. Remember, you must slip the reassembled battery back into this tube and seal the ends as they originally were, take your time and just be careful.

Figure 1. A Faraday e-Bike Lithium Ion battery.

Battery End
B – the end-cap

Figure 2. Use a fine toothed hacksaw to create a ridge along the battery cylindrical body, and the flat end cap.

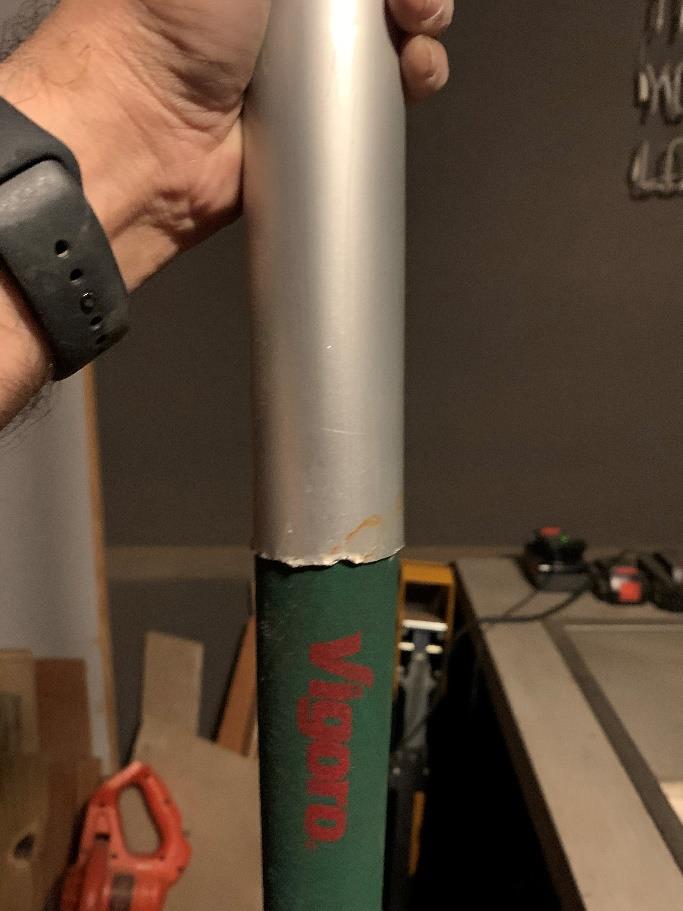
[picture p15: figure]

There are two end-caps, one on either end of the battery, that are mostly identical except that one end-cap (A) serves as a conduit for the 2 cables that exit the battery. The thicker cable supplies the power from the battery to the bike. The thinner cable is used by the Faraday controller to monitor the battery vitals, and make sure that the battery is in proper working order and that it’s not too discharged to ride the bike. Li-ion batteries are incredible finicky and its only using lots of modern controller technology that make the batteries practical. When creating the ridges, make sure that you don’t cut it too deeply. At most you need something like 1mm. You don’t need to go in any deeper, and you should be especially careful on the end-cap A where you need to keep the cables intact and avoid making any cuts into them.
Once both end-caps are out, you next task is to gently but firmly push the battery cells out from end B to A. A wooden broom end that’s narrower than the battery helps but any suitable non-metal cylindrical object of the right length and slightly
narrower than the battery tube will work.
Unfortunately, this isn’t an easy process as the

battery as such was not meant to be disassembled and contains silicon adhesives. But with some firm pressure you should be able to wiggle the contents out. Don’t tap the end using a mallet as you’re pushing against the battery controller heatsink plate and you don’t want to damage it. Just apply constant pressure and once you the contents come out of the other end, you can rotate it around to break away of the internal adhesives.

And once you’ve done that, you’ll have come to the end of the first (of many difficult) challenges in your Faraday battery rebuild. It should look something like the blue shrink-wrapped object in Figure 5.

Figure 4. A broom end serves well the push the contents of the battery out. Insert the broom handle into the end that

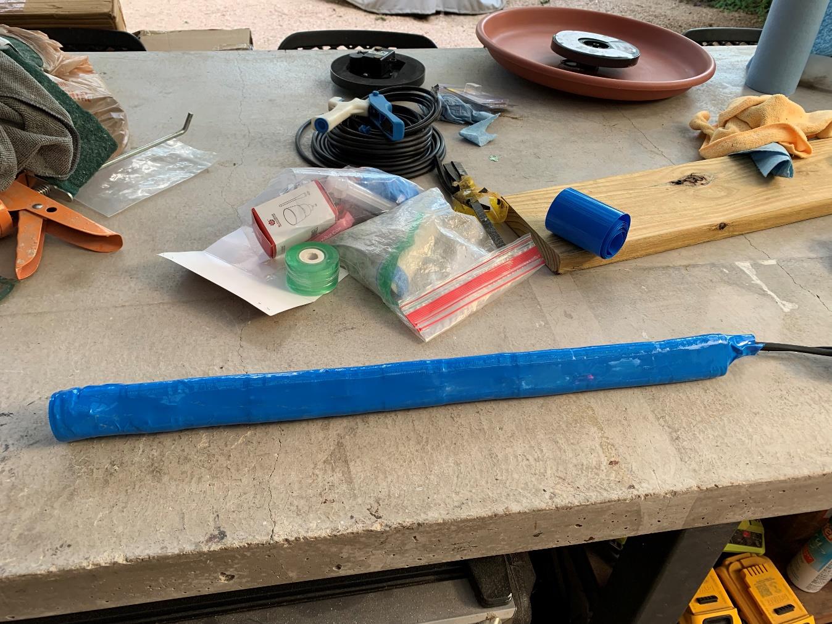
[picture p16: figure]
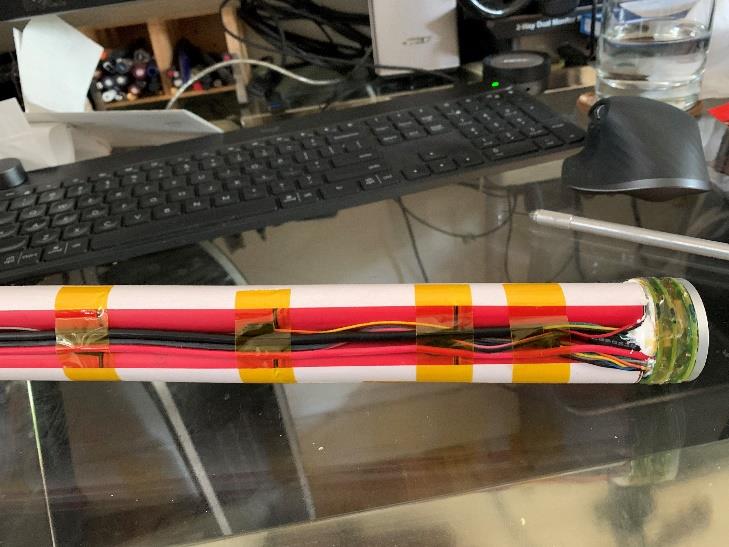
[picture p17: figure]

Figure 7. Another view of the naked battery | Figure 6. Faraday battery with blue shrink wrap removed.

Figure 5. The battery innards with the outer aluminium tube removed.

At this stage, you can carefully peel away the blue sheathing to reveal the cells inside, which should look like Figure 7 and Figure 6

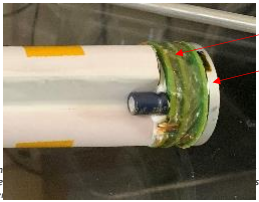
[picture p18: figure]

Figure 8. The Battery Controller or BMS is visible on the right end of this picture

At this point, you should take as many pictures of the battery as possible. How the cables are placed and routed, how the cells are laid out, how they are taped together etc. This is crucial you remember this as the next few steps will be to de-solder the wires. DO NOT CUT any of the wires. All the wires are of the precise length, and it makes things harder if you must extend a wire that you cut. But at this stage, you should just take a break and just admire the battery that you will now attempt to recreate.

## Part 3. Understanding the Construction of the Faraday battery

Before we go any further, let’s take a moment to understand the battery construction. In many respects there is nothing particularly special about a Faraday Li-ion battery that would differentiate it from a regular Li-ion battery. So what you are about to learn will also serve to help you disassemble other Li-ion batteries if you so choose, but I digress.

Roughly speaking, a Faraday battery has 5 parts

1. Outer aluminium shell or casing (the part that you just removed in order the expose the cells inside)
2. Insulation and various types of tape. The white paper tape serves as a structural component and provides some rigidity that helps maintain the shape of the battery. The Orange plastic tape is a special type of tape known as “Klapton” tape and is used widely in electronics where you need some electrical insulation as well as some thermal protection. It’s insulation isn’t as good as regular electrical tape, but regular electrical tape is much thicker so avoid using it here.
3. The wires or “Harness” – this refers to the bundle of electrical wires you see all over the battery. We will need to carefully remove the harness with a soldering iron. I’ll go over the entire process in the next section. The harness has a few different functions a) Supply current to bicycle motor
b) Charge the battery, and c) Monitor the batter function and ensure that its not overheating or depleting any of the cells beyond a “safe” limit. Notice that the wires occupy the “ridges” and this is critical to adhere to as you rebuild.
4. The Battery Controller, or Battery Monitoring System (BMS). That’s the clever part of the battery that does all the monitoring of the battery cells, voltages, currents, temperatures etc. Usually this is bulky, but the Faraday engineers managed to create a very compact unit and that’s what you see in Figure 8 on the right side. The 3-layered circuit-board sandwich is a very smartly designed controller that neatly fits together with the Li-ion cells. The aluminium disc a the very far right serves as a thermal “heat sink” i.e. absorbs heat from the power electronics and dissipates it so the temperatures remain within the working range for the devices.

Heat sink

Battery Controller

5. The Li-ion cells that stack up to create the battery. The Faraday batter consists of 12 cells connected in series, but due to the lack in space in the bicycle, the battery engineers had to come up with an ingenious way to do this. Although visually the battery looks like a stack of 8, with each stack comprised of 3 cells, that is not how the cells are electrically connected.

A simplified electrical view of the Faraday battery is shown below – 2 cells connected in parallel and

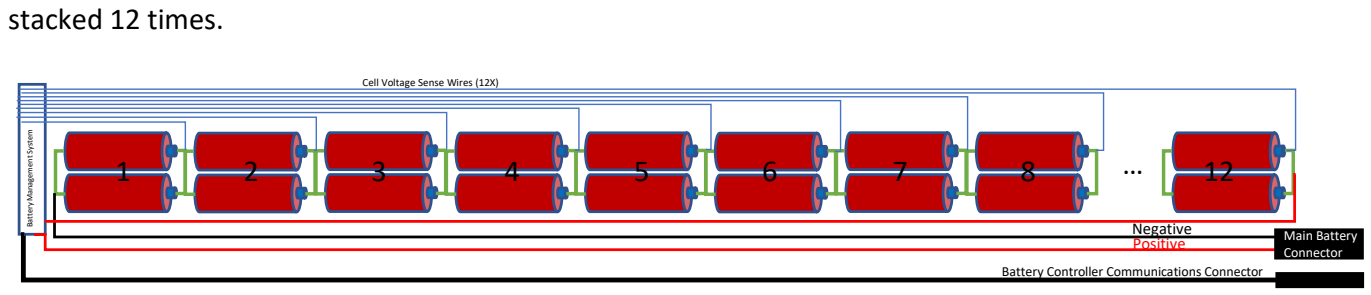
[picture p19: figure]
stacked 12 times.; Negative Positive; Battery Management System; Cell Voltage Sense Wires (12X); Main Battery Connector; Battery Controller Communications Connector

Figure 9. Simplified view of a Faraday Li-ion battery.

Even though stacking 12 high would simplify the battery construction, unfortunately the length could just be too long. Instead, the Faraday battery is constructed into 2 sections as shown in Figure 10 : Section 1 is 2 cells in parallel stacked 8 times, and Section 2: Two cells in parallel but laid out facing each other, stacked 4 times. Hence, we arrive at the electrically equivalent but with a modified battery geometry that allows us to get create a shorter battery with more girth.

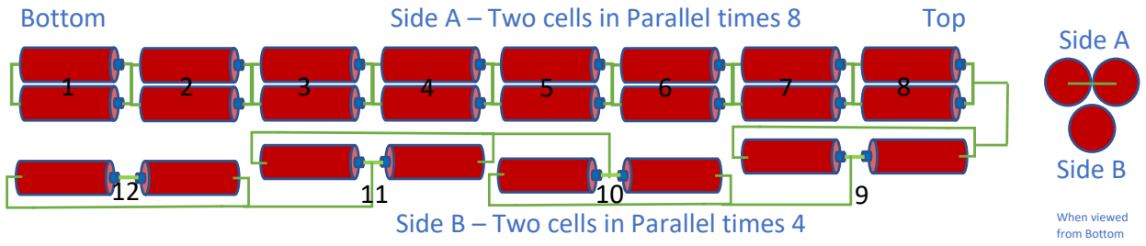
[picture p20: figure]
Side A; Side B; When viewed from Bottom; Side A – Two cells in Parallel times 8; Side B – Two cells in Parallel times 4; Bottom; Top

Figure 10. Physical layout of Faraday Li-ion battery cells

The next step is removing the wire harness and the battery controller from the cells, and this includes the Voltage Sense Wires (12), Positive Wire (1), and Negative Wire (1). We will tackle that in more detail in the next section, but as we go about doing this, you need to bear a few things in mind.

- Do not cut ANY wires. The wires are at the exact length we need them to be at and extending any wire adds insulation etc. there just isn’t any room for anything that’s not in the original battery.
- The battery controller is the brains of the battery, so be very careful in handling it. But more so, make sure you don’t do anything that can cause an inadvertent electrical short circuit. The battery controller is delicate and if you fry it for whatever reason, you can kiss the rebuild project goodbye. You will have to redo all steps with a different Faraday battery. This becomes critical in the last step of the build where you’re trying to fit everything back into that aluminium tube that encased the battery.

- Unless you are an inveterate Li-ion battery expert, at no point make the mistake that you can do something different or better. I’m a fairly competent electronics engineer and I made this mistake which cost me a battery. You’re trying to re-make the battery as is, and as long as you think along those lines, you’ll be fine.

## Part 4. Disassembling the old battery – Disconnecting the Wire Harness

Tools Needed: 45W or 60W Soldering iron.

Disassembly is probably an overstatement as most of the physical battery disassembly would have already been performed if you’ve removed the aluminium tubing. This stage is where you separate the battery controller, along with the voltage sense wires from the battery itself.

Just as reminder again, you are not going to cut any of the wires. Why? Because they are already at the exact length, and you merely want to de-solder them from their existing connections.

To be precise, you should exactly 14 wires to de-solder as follows.

- 14 voltage sense wires (shown with red circles in the images below)
- 7 on side A connected via narrow tabs

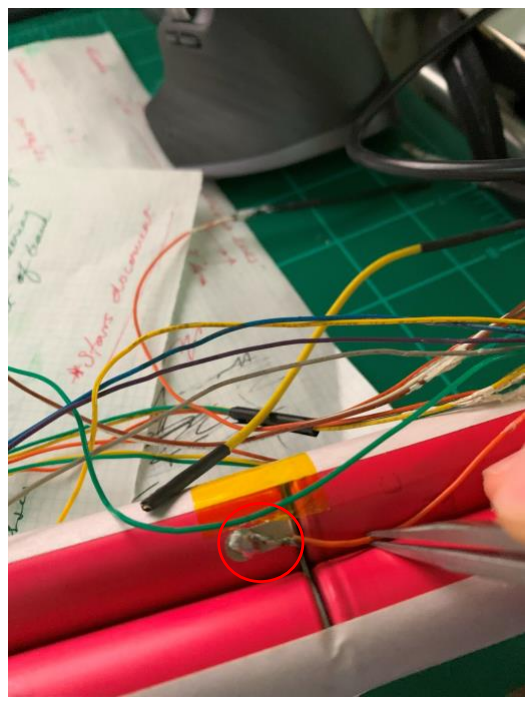
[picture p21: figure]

Figure 11. Voltage sense wires on Side A are connected to narrow tabs with very narrow wires. A soldering iron will help you disconnect the wires easily.

- 5 on side B connected via broad tabs

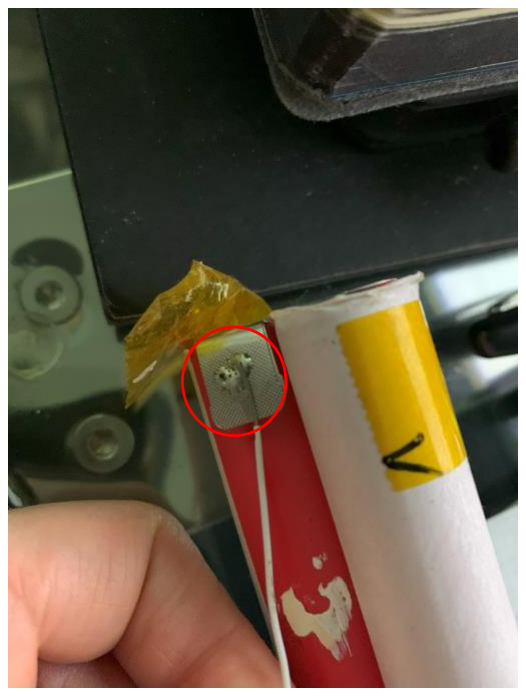
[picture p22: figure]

Figure 12. Side B Voltage tabs use broader tabs.

- 1 on side B connected at the bottom via a narrow tab (electrically connected to battery -ive terminal)

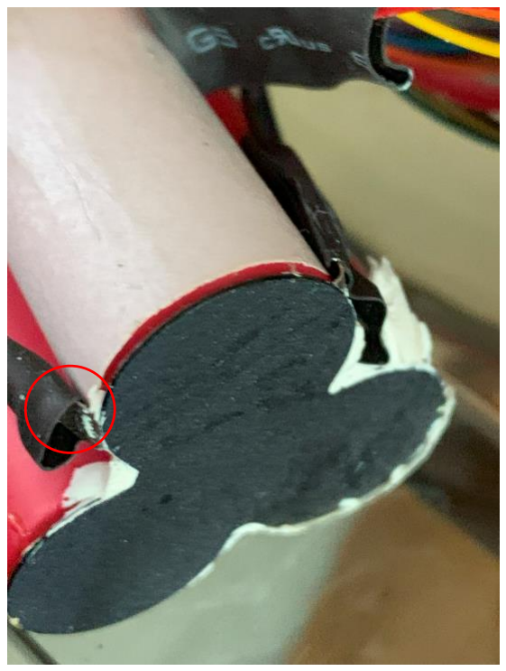
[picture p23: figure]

Figure 13. The voltage sense wire is on the left-hand side in the picture above soldered to a narrow tab.

- 1 on side B connected with the +ive connection

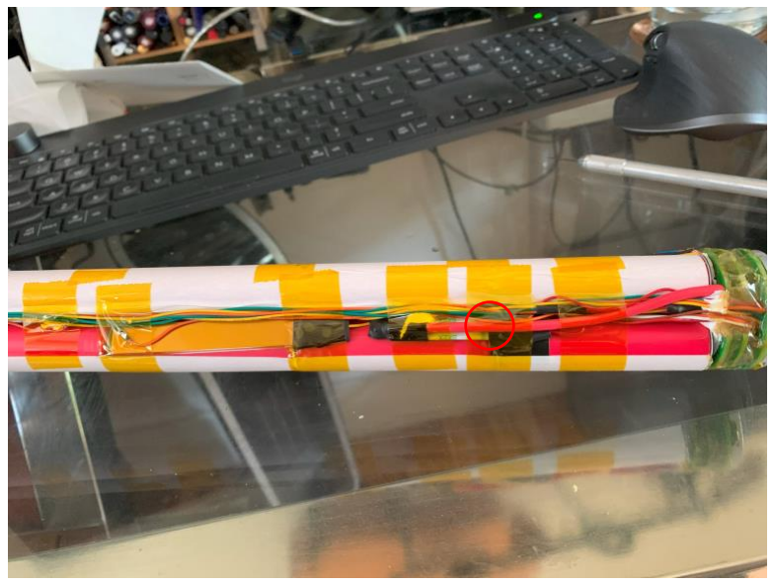
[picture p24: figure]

Figure 14. The +ive wire (thick) red, is connected to the battery +ive through a metal strip

- Battery -ive (Side A bottom)

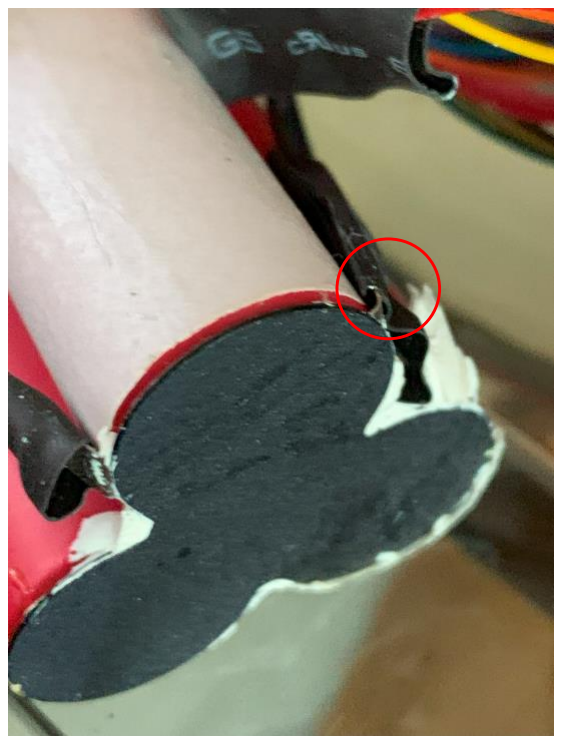
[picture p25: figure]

Figure 15. The -ive wire (thick) black is connected to the battery -ive through a wide tab.

- Battery +ive (Side B) – Desolder the fat red wire and metal strip from the battery tab as shown in Figure 16 with the red circle. Do not desolder the metal strip from the thick red wire.

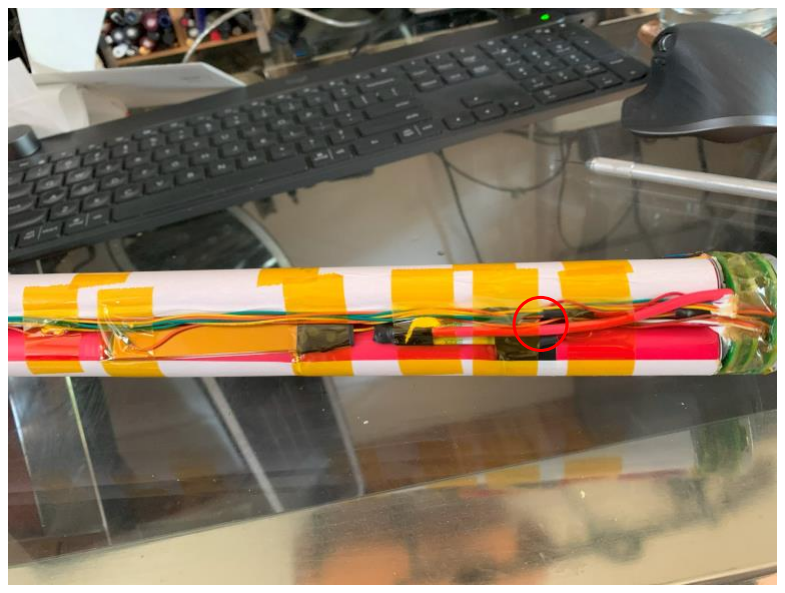
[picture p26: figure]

Figure 16. The +ive wire is soldered onto a metal strip. The metal strip is then soldered onto a tab on the battery. You want to keep the metal strip connected and desolder it from the battery tab. It’s somewhat hidden in the picture above but you should be able to identify it. I’m not quite sure what purpose the metal strip serves.

In addition, you will notice that there a few wires on side B that are glued on. These are temperature sensors (also known as thermistors) and there are 4 of these.

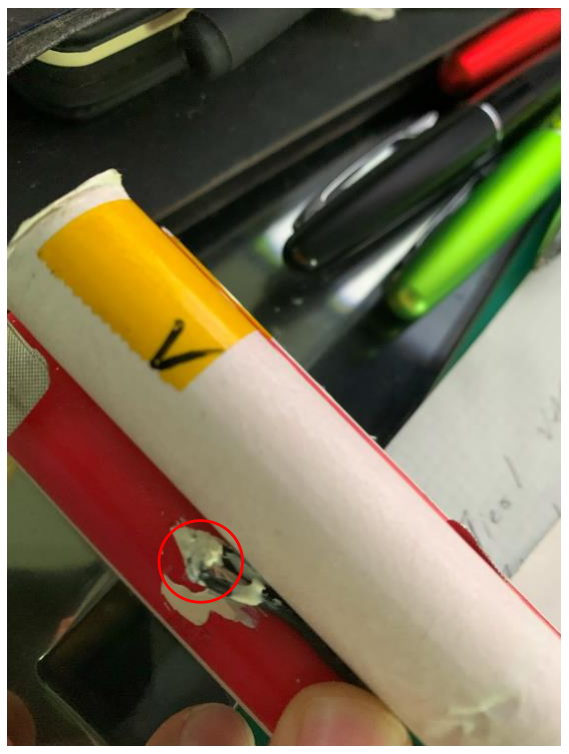
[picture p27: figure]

Figure 17. Notice the temperature sensor. It is held in position with thermal glue (white) that you can easily pry off.

You can gently pry them out. Don’t pull on the wires as those will break easily and my guess is that the battery controller will refuse to work if it doesn’t detect them. So again, be very careful.

But before you start separating the battery controller, pay close attention to its orientation with regards to Side A & B. On reassembly, you will need to make sure that its oriented exactly the same way. The capacitor below serves as a great reference point in Figure 18

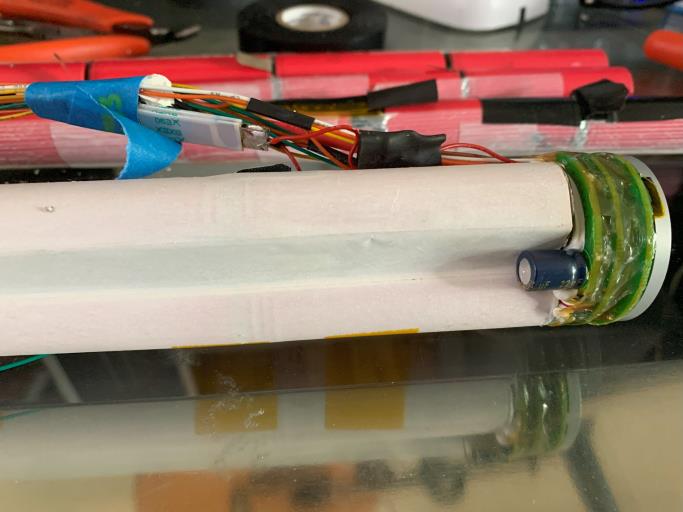
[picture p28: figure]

Figure 18. You'll want to keep orientation of the battery controller in mind when reattaching the battery controller.

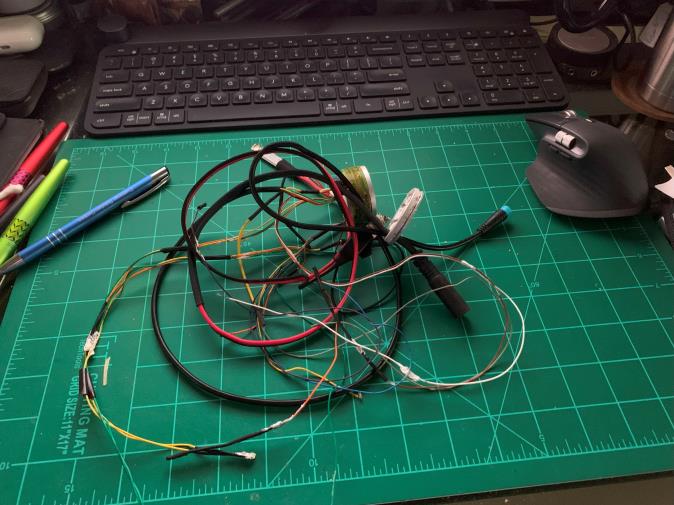
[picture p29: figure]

Figure 19. The separated wire harness and battery controller

At this point, you should be able to separate the wire harness from the li-ion cells as shown in Figure 19. You are going to reuse the harness so store it carefully.

Also keep the (spent) li-ion battery handy as a building reference, not only as a visual guide on where the various tabs need to be placed, but also from a dimension perspective. You want to make sure that your battery adheres to the dimensions (both length and girth) exactly.

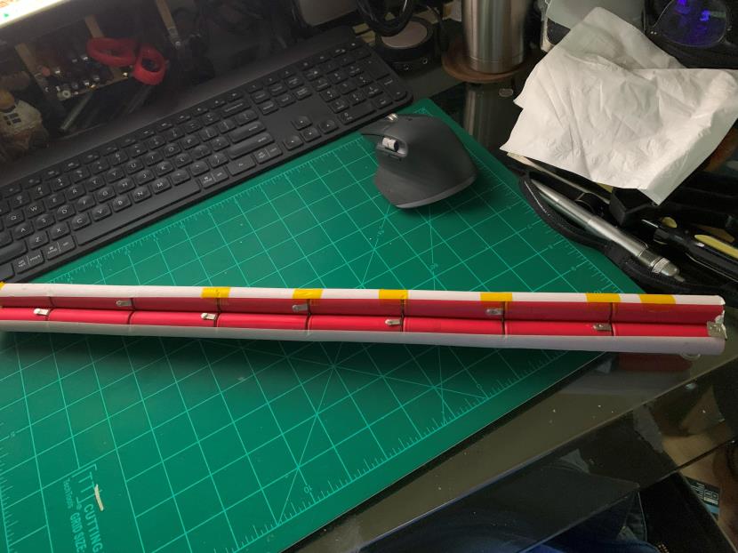
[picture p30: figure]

Figure 20. Keep this handy as you'll want to refer to this as you build your new battery

## Part 5. Building a new battery

Before you start assembly, please make sure you take a good look at the old one. The tab placement is crucial, but also how sides A and B are placed together.

Of the 3, Grooves 1 and 3 are the most important because they serve as a channel for the various wires as shown in Figure 22, Figure 23 and Figure 24.

Side A

Side B

When viewed
from Bottom
Groove 3 | Groove 2 Groove 1

Figure 21. Identifying the various grooves on the battery

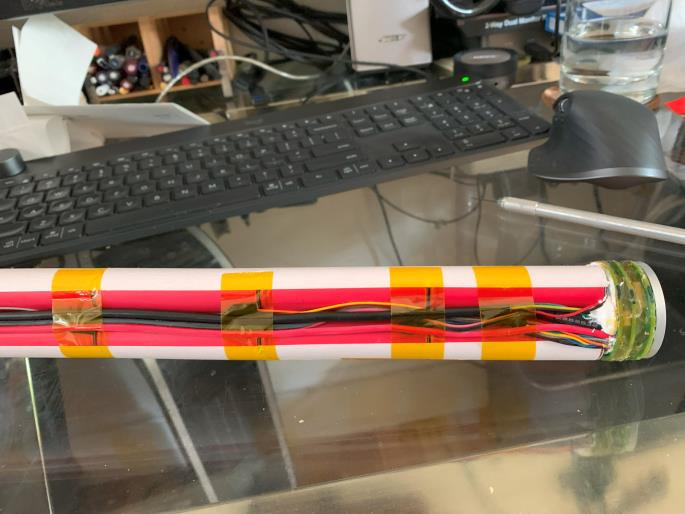
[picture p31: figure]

Figure 22. Groove 1 on Side A – Notice this contains the voltage sense wires, as well as the wires (thick) that lead to the external connectors.

Figure 23. Groove 2 - Notice the placement of the capacitor in the battery controller

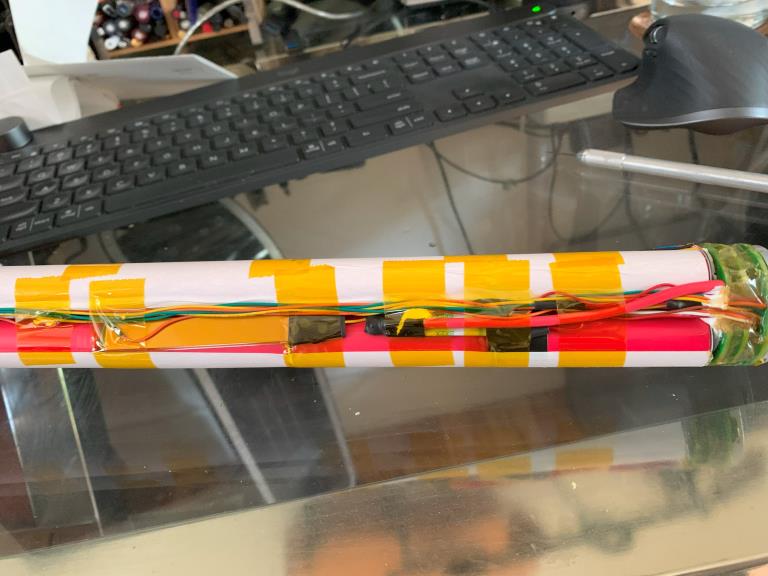
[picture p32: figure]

Figure 24. Groove 3 - Notice how the voltage sense, temperature sense, and the thick red +ive wire are all housed in the groove

We are going to build the battery in two parts namely, Side A & Side B. As a reminder, Side A is comprised of the two cells in parallel stacked 8 high as shown in Figure 10, and Side 2 is comprised of slightly different layout where the 2 parallel cells are laid out linearly, and then stacked 4 high.

To make the construction easier, we will build each side independently, and then combine them together.

You will notice that the factory battery has pre-cut nickel tabs that they weld onto the battery. Unfortunately for us, we can’t access those pre-cut tabs and instead we will have to fashion our own from strips of nickel.

### Building Side A

This part is simple and straightforward – not it can get a bit unwieldy especially when you have all 8 cells in place. I approached this by constructing 4 sets with 2-banks of cells in each.

Step 1.

Make the following connecting surfaces from 0.1mm x 6mm pure nickel. Please make sure all edges are rounded off.

Follow the diagrams below to spot weld the various nickel tabs onto the li-ion cells as follows

1 | 2 | 3 | 4 | 5 | 6 | 7 | 8
1 | 2 | 3 | 4 | 5 | 6 | 7 | 8

30mm

Type 1a | 6mm

15mm

Type 1b 3mm

55mm

Type 1c | 6mm
Make 3 of this | Make 8 of these | Make 7 of these

Spot Weld

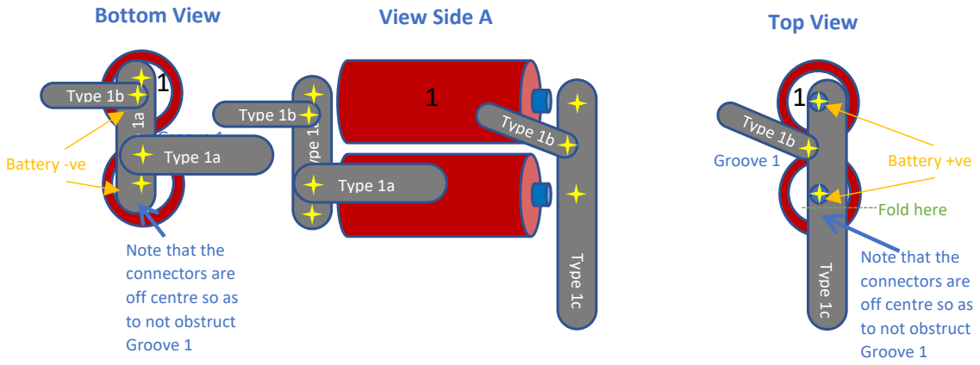
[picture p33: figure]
Type 1a; Type 1c; Type 1b; Bottom View; View Side A; Top View; Battery -ve; Battery +ve; Fold here; Groove 1; Note that the connectors are off centre so as to not obstruct Groove 1

Step 2. Fold the Type 1c connector and spot weld to cell bank 2 as shown below. It’s a bit tricky since you must keep the bank 1 at an angle. A second set of hands will be helpful here.

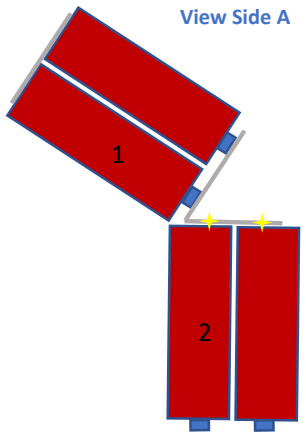
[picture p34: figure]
View Side A

Step 3. Connect the remaining cell banks in a similar in groups of two. Note the Type 1b tabs (battery voltage sense tabs have an alternating offset pattern. Banks 3-4, 5-6 are identical. Bank 7-8 is also very nearly identical except for the Type 1a tab at the end.

View Side A

3

Type 1b

4

Type 1c
Folded

Type 1c
Folded

View Side A

5

Type 1b

6

Type 1c
Folded

Type 1c
Folded

View Side A

7

Type 1b

8

Type 1c
Folded

Type 1c
Folded
Type 1a

Spot Weld this
Type 1c tab to
Bank 1-2

Spot Weld this
Type 1c tab to
Bank 3-4

Spot Weld this
Type 1c tab to
Bank 5-6

At the end of the following steps, you should have the following Side A battery in place, but with all the proper tabs in place etc. Again, always use the original battery to make sure you have ALL the tabs in their required places. Also pay attention to the direction of how the tabs are folded – it is done to ensure that you don’t have accidental shorts. Again, you want your battery to look EXACLY like the original as much as possible. The nickel tabs themselves aren’t very strong as I’m sure you’ve noticed as you build banks 1-8. You will have to use paper tape to give the banks some mechanical structure and stability. Again, don’t be tempted to use duct tape as its too thick and you won’t be able to slide the battery into the aluminium tube.

### Building Side B

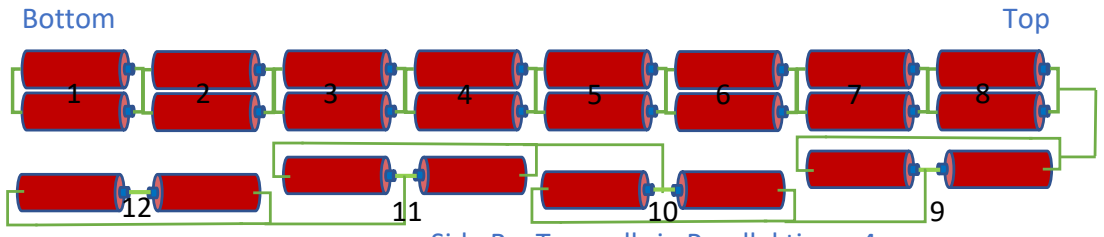
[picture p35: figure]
Bottom; Top

Side B construction is a bit more tricky compared to Side A as you can see in the image above. The good news is that it uses a repeating pattern that we can use to make build a bit easier. The bad news is that spot welding can be a bit more challenging since you are working in tight spaces. We will be using 0.15x8mm pure nickel strips for making these connectors. There is a lot of potential for shorting in this stage so as always make sure the +ive terminals never come into contact with the -ive terminals. A good practice is to temporarily insulate an ends

Side B – Two cells in Parallel times 4

Step 1: Put a layer of the Kapton tape on both sides of the connectors. Here is a picture of the original battery which shows the Kapton tape sandwiching the connector. This is to insulate it. Ordinary electrical insulation tape won’t do as its too thick. Leave a small portion of the end exposed so you can spot weld to the cell terminals.

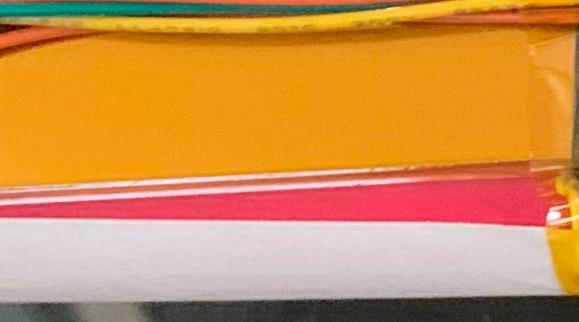
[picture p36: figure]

Place 2 cells with the +ive facing each other. Use a Type 2b connector, and spot weld to the -ive terminals of each cell as shown below.

110mm

Type 2a | 8mm

Make 3 of these

130mm

Type 2b | 8mm

Make 1 of these

160mm

Type 2c | 8mm

Make 3 of these

30mm

Type 2d | 8mm

Make 1 of these

40mm

Type 2e | 8mm

Make 1 of these

Stick to top side of Nickel Strip

Stick to bottom side of Nickel Strip

Cross section

Step 2: Use type 2 connector, fold one end into a V and spot weld the battery +ive to each leg of the V
Step 3: Banks 10, 11 and 12 are fairly similar, except that you will use the Type 2c connector instead which are slightly longer and will give you bit of an overhang that you will need to connect with the other battery banks. Follow Step 2 to connect the Type 2a connectors for each of the battery banks 10 to 12 as shown below.
Step 4: For battery bank 12, spot weld the Type 2e connector. This is where the Battery Controller +ive wire will eventually connect to.

9

Type 2b

0.3mm

10

Type 2c

0.3mm

11

Type 2c

0.3mm

12

Type 2c

0.3mm

Step 5: At this point, you should have 4 separate battery banks 9-12. In this step, we’re going to connect those banks together. The batteries can be a bit unwieldy, so use paper tape as a temporary aid to give it some structural stability. First connect banks 9 and 10 together as shown below.

Warning: Don’t forget to place an insulator disc in between the battery banks as shown by the BLACK line below. You have to do this between battery banks 9 & 10, 10 & 11, and 11 & 12.

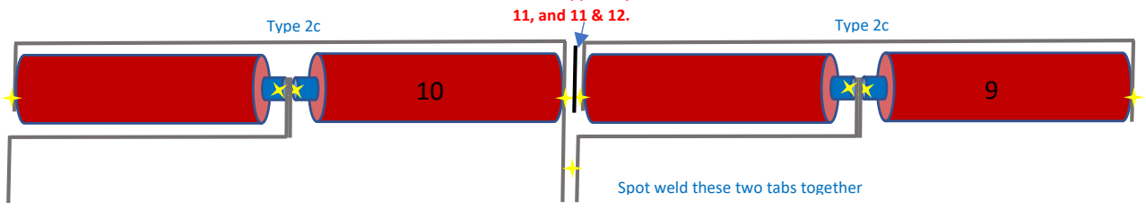
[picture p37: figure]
Type 2c; 11, and 11 & 12.; Spot weld these two tabs together

Follow step 5 for connecting bank 11, and then bank 12.

Step 6: At this point you should have the completed the 2 parts of the battery i.e. Side A and Side B, however they are electrically disjointed. We connect them together in the final spot weld using a Type 2d connector.

First, place Side A and B so that Side A banks 1 & 2 align with Side B bank 12. Side B nestles into the groove of Side A to form a triangle. You can use paper tape in Groove 2 to attach Side A and B together. You can then spot weld the Type 2d connector to Banks 8 and 9 as shown below.

Important: Place a suitable insulator disc here. Bad Things WILL happen if you fail to do so. Also DO this in between 10 &

Type 2b

Type 2e

12

Side A

Side B

When viewed
from Bottom
Groove 3 | Groove 2 Groove 1

## Part 6. Putting it all back together

If you’ve made it thus far without burning your house down, then hearty congratulations are in order! The last few steps are walk in the park compared to everything you’ve been through so far.

Step 1: Reattach the wire harness. This is essentially the opposite of Part 4, so you have to follow the same steps in reverse order. Remember to align the capacitor on the battery controller to Groove 2 at the bottom of Battery Bank 1. Re-solder back voltage sense wires.
Step 2: Reattach the +ive and -ive wires to battery bank 12 and 1 respectively.
Step 3: Place the temperature sensors at Battery banks 9-12 and use thermal paste to stick them in place.
Step 4: Place the wires so that they fit neatly in the respective Grooves 1 and 3. Make sure all the insulation matches the original battery. Also make sure that at no point is the battery and wires wider than the width of the aluminium tubing. Making a cardboard cutout of the aluminium tube with the same diameter and slide it over the length of the battery. If anything is jutting out and tuck it in as neatly as you can.
Step 5: Insert the battery into a heat shrink tubing and use to heat gun to shrink the film and hold everything in place.
Step 6: Check the dimensions of the shrink-wrapped battery to ensure that it’s smaller than the diameter of the aluminium tubing.
Step 7: Remove any sharp edges in the aluminium tubing. You might want to slightly flare out one of the ends to make it easier to slide the battery inside.
Step 8: Carefully slide the battery inside the tubing. Do not force it excessively at any point, since too much force will likely tear any insulation inside and the battery could short and start smoking. At this point having a fire extinguisher is a necessary safety precaution.
Step 9: Replace metal end-caps.

Congratulations, at this point if all is well, you should be able to slide your new battery into your Faraday bike, connect it and all should work as usual.

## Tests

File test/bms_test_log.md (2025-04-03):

# for branch BQ-refactor

Listing out the functions of the BMS and when/what was tested

| Function  |  What?  | When tested|
|---|---|---|
| Overvoltage |  Prevent cells from overcharge | verified 3/24/2025 |
| Undervoltage |  Prevent cells from undercharge | verified 3/25/2025 |
| Charging Overtemp Cutoff| prevent cells from charging beyond their rated temperature  | Verified during soldering of PCB 3/23/2025|
| Charging Undertemp Cutoff | prevent cells from charging below their rated temperature  | Verified with 30 minute freezer test 3/26/2025 |
| Discharging Overtemp Cutoff| prevent cells from discharging above their rated temperature  | Verified during soldering of PCB 3/23/2025|
| Discharging Undertemp Cutoff | prevent cells from discharging below their rated temperature | Not yet verified |
| Deep Discharge Lockout |prevent deeply discharge and possibly damaged cells from being charged  | Not yet verified|
| Overcurrent | turn off immediately when a short circuit occurs  | Not yet verified |
| Overcurrent in Charge | turn off immediately when excessive charge current is applied | Verified 3/24/2025 |
| Overcurrent Backup  | 25A, 75V Fuse  | prevent shorting batteries if software and BQ chip fail somehow  | Not yet verified |
| Balancing in CHARGE and RELAX | Keep cells with a few mV of each other| Verfified via DEBUG command 3/24/2025 |
| DEEPSLEEP sleep state | Minimize power consumption while off. BQ goes into DEEPSLEEP, STM32 goes into STOP modes| Not yet verified |
| SHUTDOWN sleep state | Dramatically reduce power consumption between 0% SOC and bricking voltage to extend life| Challenging to verify|
| Wake on insertion of charge plug | Mirror original faraday behavior| Verified 3/24/2025 |
| Wake on momentary pull-down of button | Mirror original faraday behavior | Verified 3/24/2025 |
| Watchdog | reset STM32 if code crashes| Not yet verified |
| Battery OK message | Responds to messages from rear controller to enable high torque mode and update screen| Not yet verified |
| Battery voltage message | Responds to messages from rear controller to enable high torque mode and update screen| Verified 3/24/2025 |
| Battery balancing message |  Responds to messages from PC debug tool| Not yet verified |
| Debug Compilation Flag | Dump lots and lots of info over serial to facilitiate debugging| Verified 3/23/2025|
| CHG and DSG LEDs | Indicate status of FETs| Verified 3/24/2025|

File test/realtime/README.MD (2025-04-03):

# Realtime Data Logging

Use STMSTudio and the programming header.

List of memory locations for the batt state struct:

| Name | Type | Address |
| -----| ----| ---|
| CellVMin | int16_t mV| 0x20000432|
| CellVMax | int16_t mV| 0x20000434|
| Current | int16_t  mA| 0x20000450|
| Temp1 Cell | float  C| 0x20000438|
| Temp2 Cell | float  C| 0x2000043c|
| Temp3 Cell | float  C| 0x20000440|
| Temp4 BQ | float  C| 0x20000444|
| Safety Status A Register | uint8_t | 0x20000454 |
| Safety Status B Register | uint8_t | 0x20000455 |
| Safety Status C Register | uint8_t | 0x20000456 |
| Permanent Fail A Register | uint8_t | 0x20000457 |
| Permanent Fail B Register | uint8_t | 0x20000458 |
| Permanent Fail C Register | uint8_t | 0x20000459 |

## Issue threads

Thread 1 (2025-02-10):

End-of-charge Spinning LED Behavior Incorrect

nhallsny, 2025-02-10:
**Describe the bug**
At end-of-charge, the spinning LED wheel should be solid. Right now, the spinning wheel of LEDs pauses on whichever LED was lit when the battery turns off.

**To Reproduce**
Steps to reproduce the behavior:
1. Plug the bike into the charger
2. Charge the bike
3. When charge is finished, only a single LED on the spinning wheel is lit

**Expected behavior**
With the original faraday battery, all LEDs are lit when charge is complete, the battery is off, and the charger is plugged in.

**Images**
Expected end-of-charge
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

**Additional context**
There is likely a message that changes when the battery turns off the CHG FET before it goes to sleep.

nhallsny, 2025-03-09:
Fixed with [C13ce70](https://github.com/nhallsny/faraday-rescue/commit/c13ce704ff4bc1c484481465890b1b623d985e95)

nhallsny, 2025-03-09:
Closed

nhallsny, 2025-03-09:
Actually closed this time, see https://github.com/nhallsny/faraday-rescue/commit/c13ce704ff4bc1c484481465890b1b623d985e95

Closed 2025-03-09.

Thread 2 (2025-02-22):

Use Permanent Fail feature on BQ to disable FETs if cell voltage drops too low

nhallsny, 2025-02-22:
**Is your feature request related to a problem? Please describe.**
Need to disable FETs permanently when cell voltage drops below 1.0V (according to datasheet, will probably use 1.9V) to prevent charging fully discharged cells.

**Describe the solution you'd like**
Set  Settings:Protection:Protection Configuration[PF_FETS] and Settings:Permanent Failure:Enabled PF A[SUV] and Settings:Manufacturing:Mfg Status Init[PF_EN] configuration bits.

**Describe alternatives you've considered**
No alternatives

**Additional context**
Add any other context or screenshots about the feature request here.

nhallsny, 2025-02-26:
Fixed in [Undervoltage lock-out and spinning LED fix](https://github.com/nhallsny/faraday-rescue/commit/bb3546d6271cda69e1ff525dc024f5ee5c2a32be)

Closed 2025-02-26.

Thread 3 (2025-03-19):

BQ ReadReg doesn't support more than a 16 Byte Transfer

nhallsny, 2025-03-19:
**Describe the bug**
The original starter code from TI had a 32 byte transfer. When used in CRC mode, this appeared to segfault the STM32.

**To Reproduce**
Steps to reproduce the behavior:
1. Try to read a 32 byte register

**Expected behavior**
Not segfault

**Images*
None

**Additional context**
This isn't needed for the faraday battery, more of a nice-to-have for the portability of the BQ769x2 library.

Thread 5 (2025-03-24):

RX485 RX not waking after return from STOP mode

nhallsny, 2025-03-24:
**Describe the bug**
RS485 not responding the battery messages after returning from stop on branch BQ-Refactor

**To Reproduce**
Steps to reproduce the behavior:
1. Wake from sleep
2. Send voltage request message
3. Observe response in Saleae Logic
4. STM32 does not respond

**Expected behavior**
STM32 should respond to RS485 messages

Closed 2025-04-03.

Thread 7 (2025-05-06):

Intermittent reduction in torque when climbing long hills

nhallsny, 2025-05-06:
**Describe the bug**
On one Faraday with replacement battery, the motor torque appears to change between low and high intermittently.

**To Reproduce**
Steps to reproduce the behavior:
1. Ride up hill
2. Feel changes in motor torque

**Expected behavior**
Motor should not change torque while riding unless commanded from motor selector

nhallsny, 2025-05-06:
Root cause ideas:
- Intermittent RS485 connection
- Dropped battery status packets
- Incorrect formatted battery status packets

First, I probed all the internal connections of the battery to verify that the wiring and crimps are good. They were.

I confirmed that unplugging the RS485 cable after the bike is on puts the bike in a limp mode of sorts. Then, I attached a logic analyzer to the RS485 line and took a trace while the stuttering was happening. I confirmed that all messages are getting to and from the battery. I have no way of telling if the rear controller is parsing the status messages successfully. However, I noticed that the reduction in torque always came immediately after the Battery Status 1, Battery Status 2, and Battery Voltage Reads. This suggests that something about the response (or lack thereof) triggered the torque reduction.

As a debugging step, I changed the payload on battery status 2 from a temperature (int16_t of hottest cell) to a hard coded value 0x19 and it appeared that the issue went away.

There are two possibilities:
- The payload of Battery Status 2 is a bitfield, not a temperature. The code was sending the wrong payload for Battery Status 2
- Removing and re-installing the battery re-arranged the cables, reducing noise on the RS485 lines. I think this is less likely...the noise on RS485 A and B was small and entirely common mode, which should be filtered out by the CM chokes and driver chips.

Next steps:
- Let the user use the bike for a few weeks to see if the problem returns. If so, update MAIN

Closed 2025-06-18.

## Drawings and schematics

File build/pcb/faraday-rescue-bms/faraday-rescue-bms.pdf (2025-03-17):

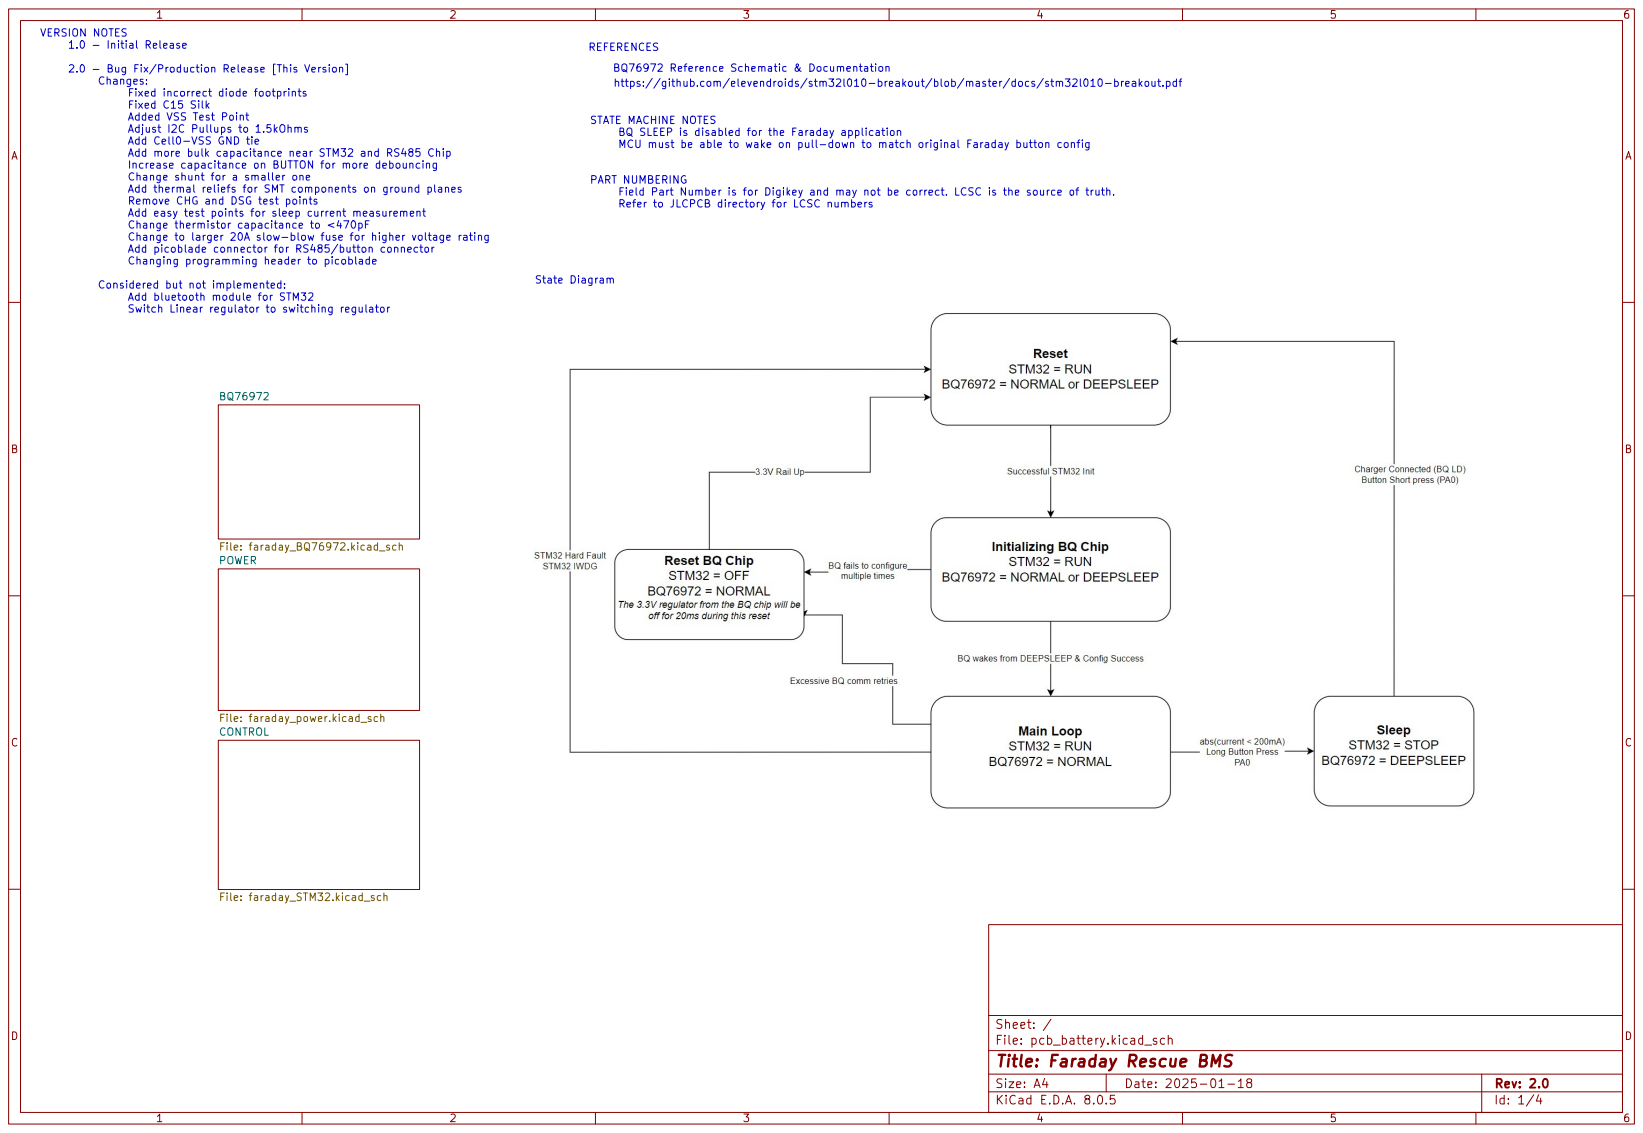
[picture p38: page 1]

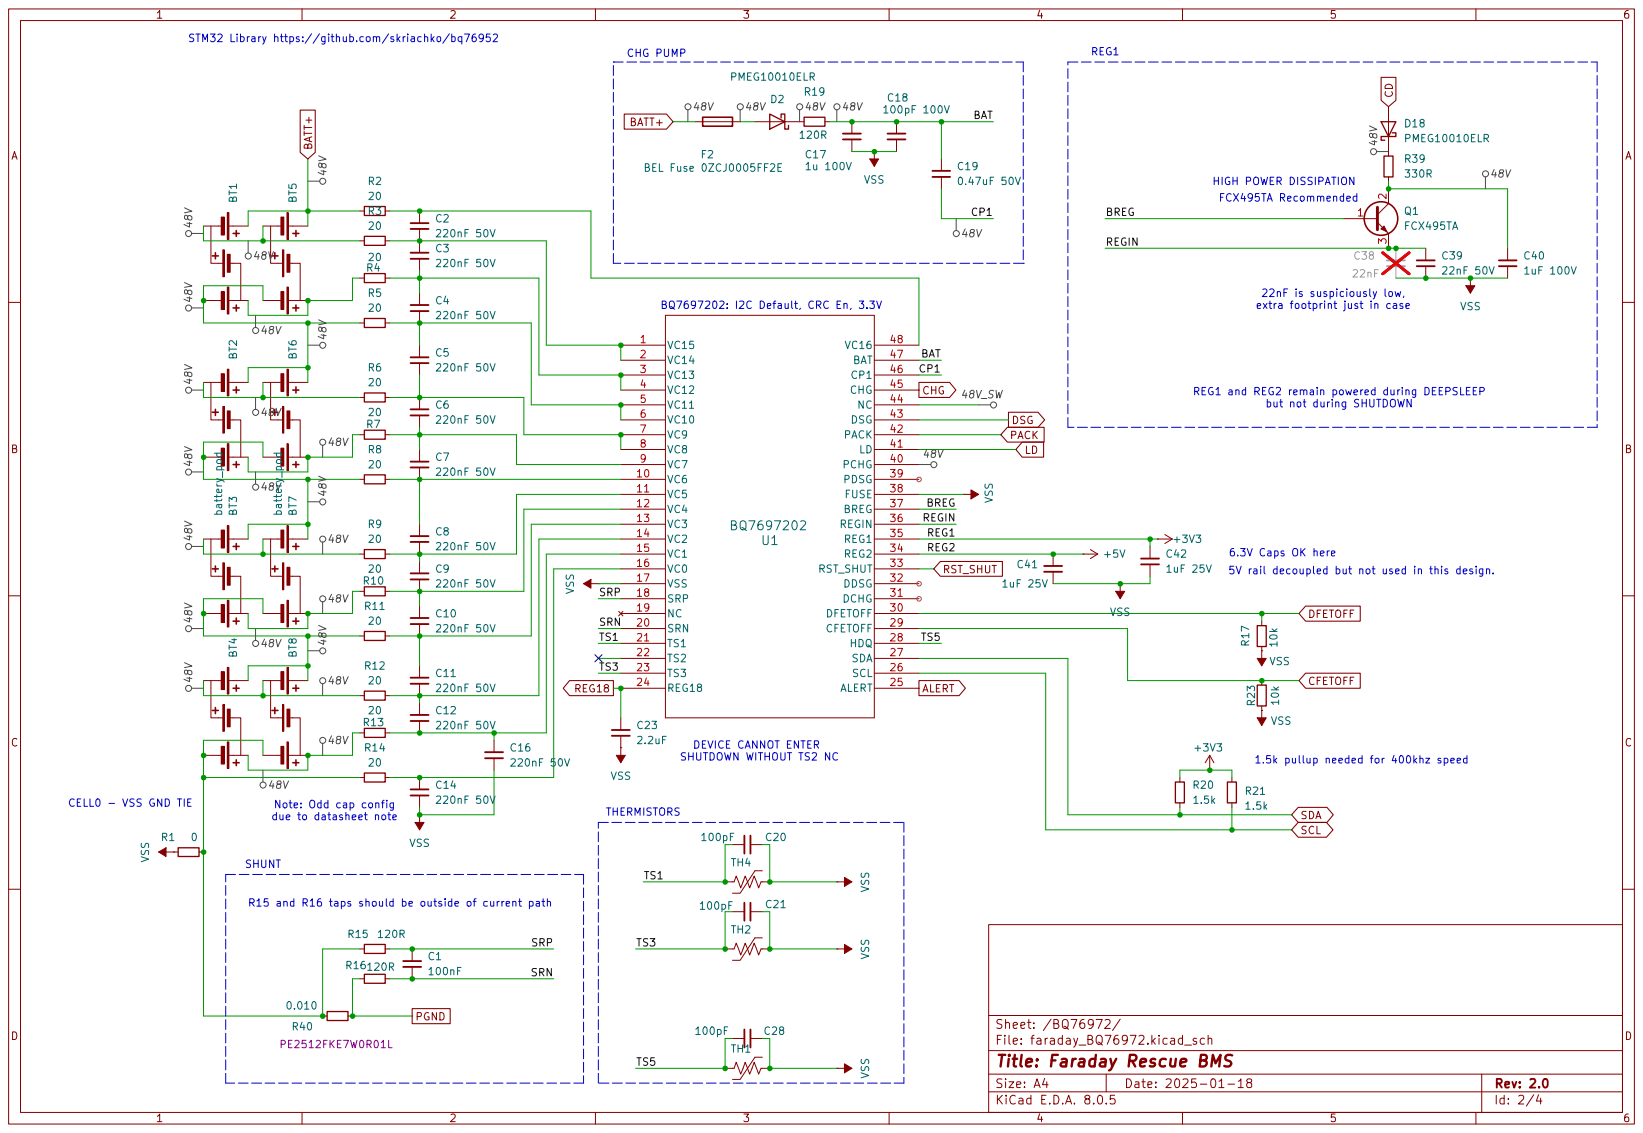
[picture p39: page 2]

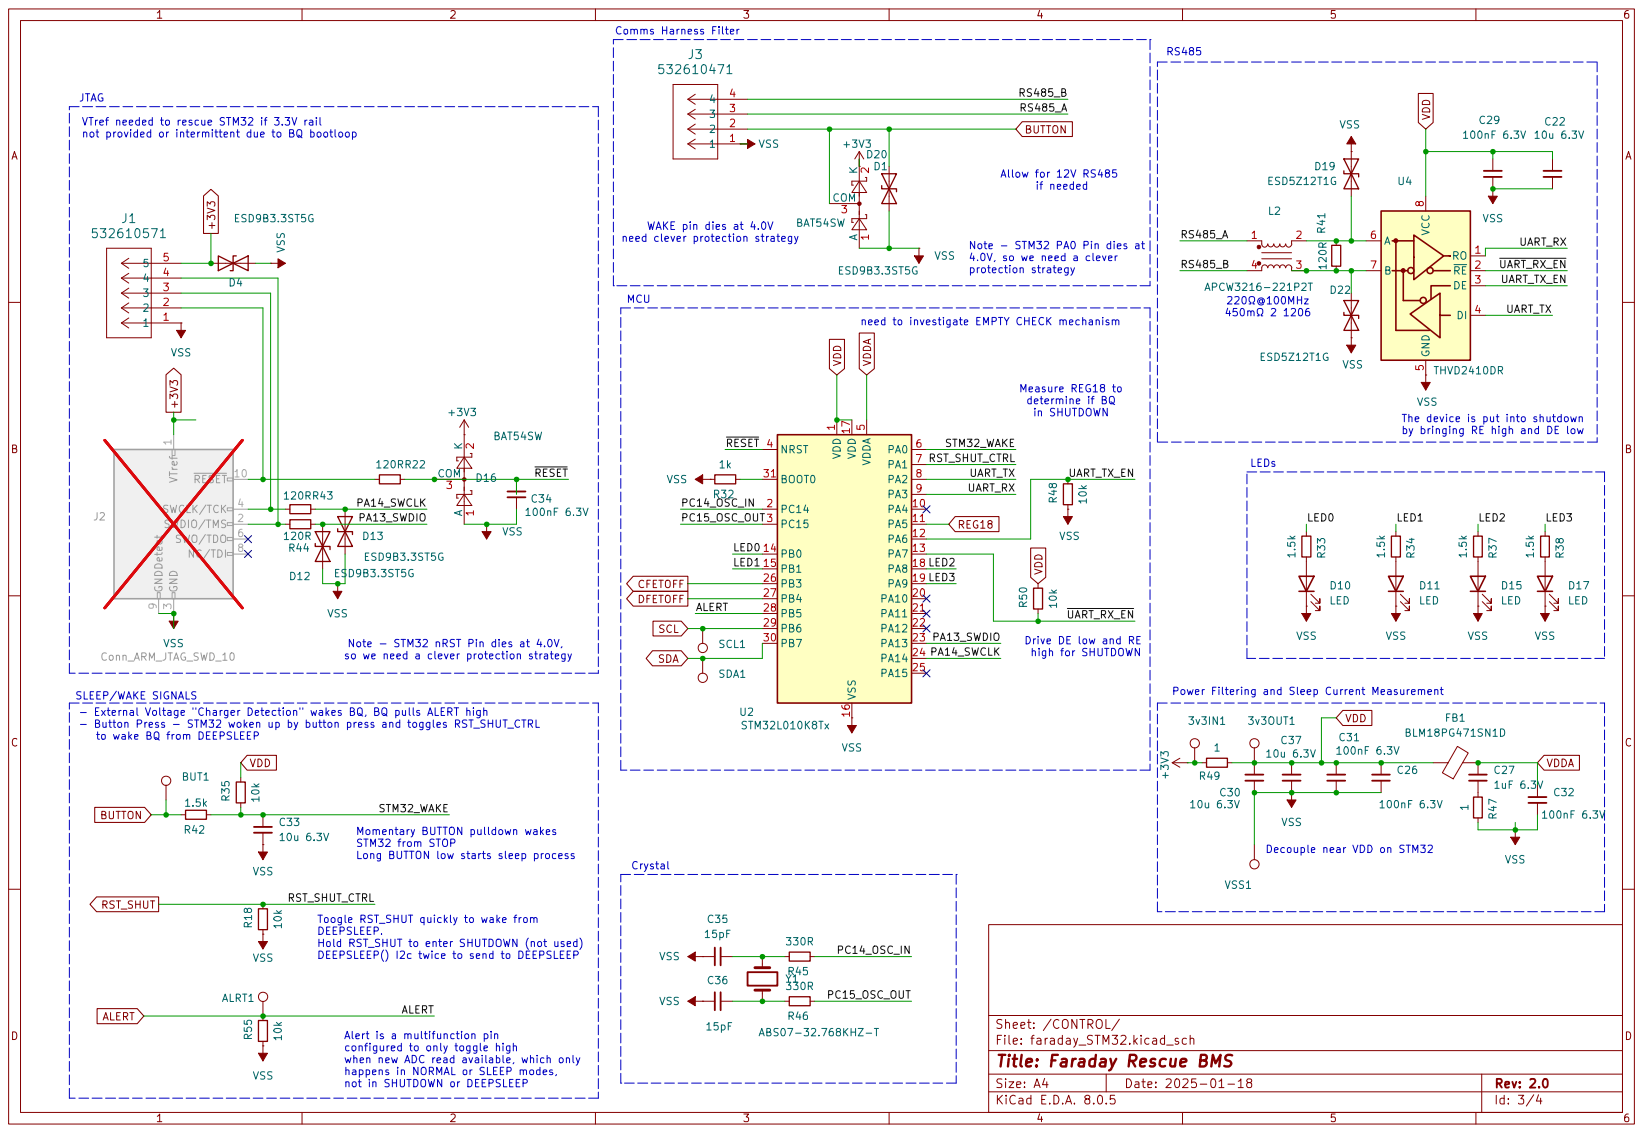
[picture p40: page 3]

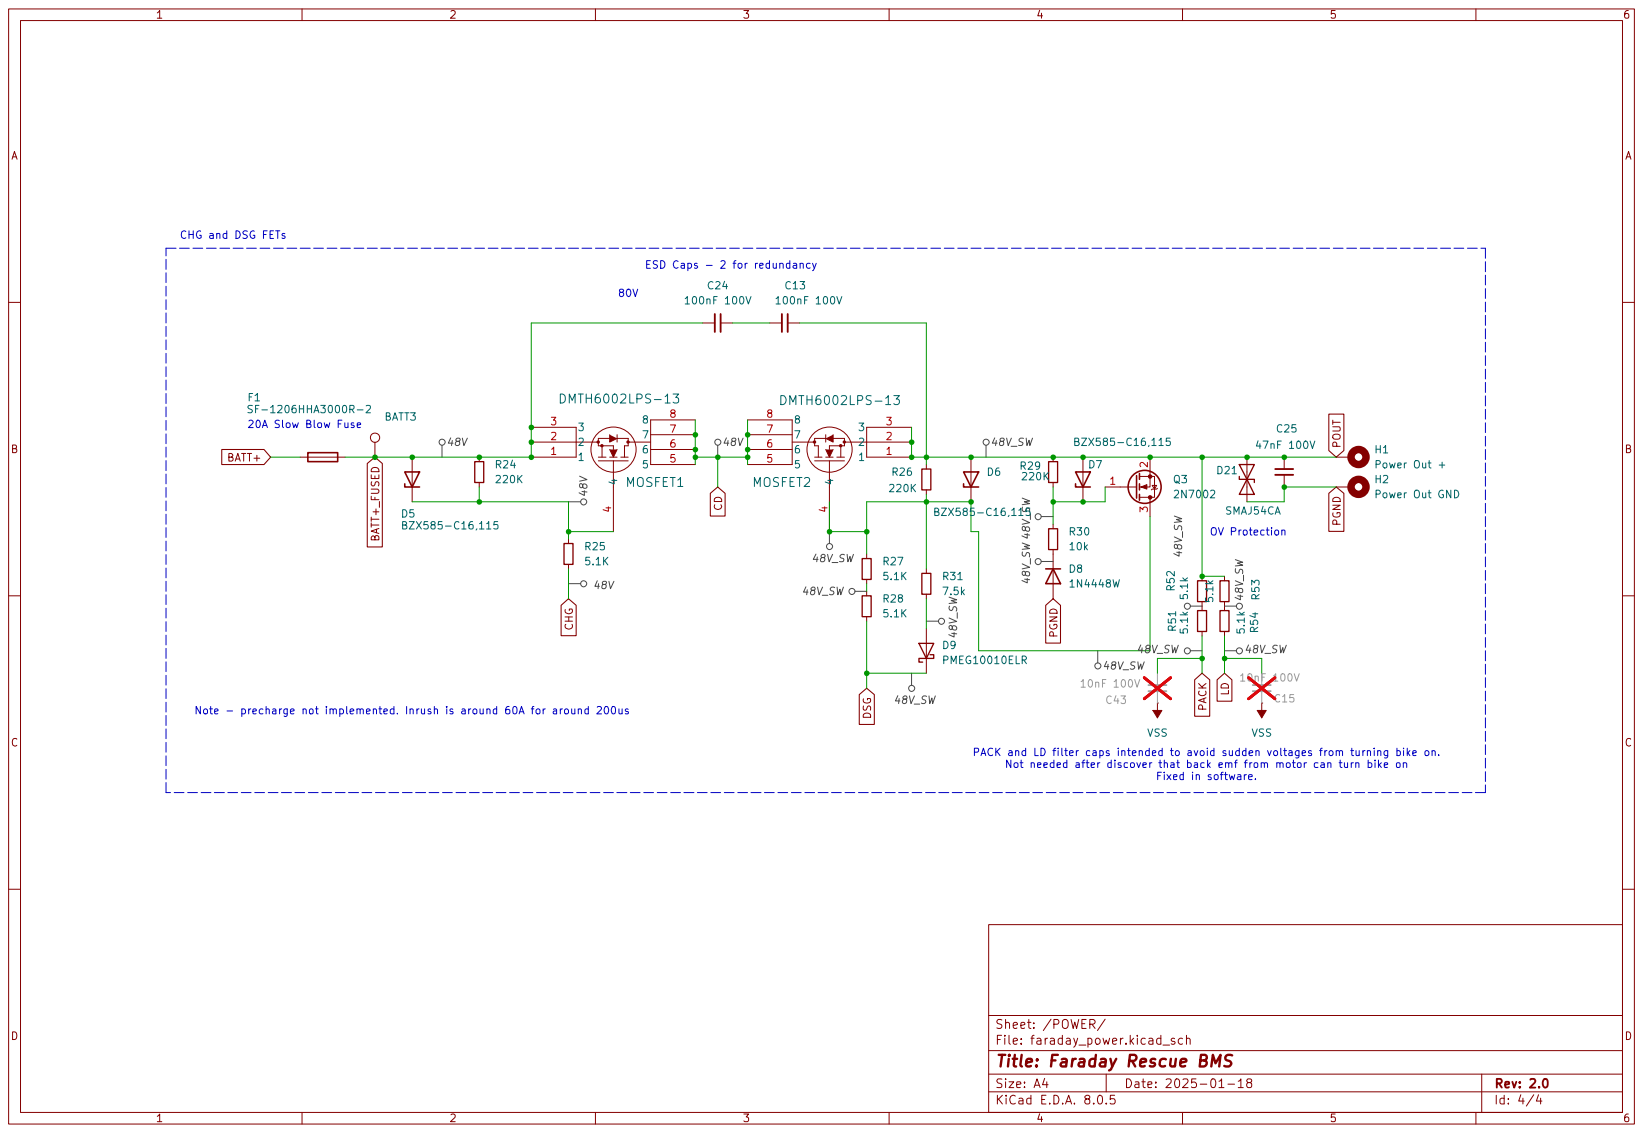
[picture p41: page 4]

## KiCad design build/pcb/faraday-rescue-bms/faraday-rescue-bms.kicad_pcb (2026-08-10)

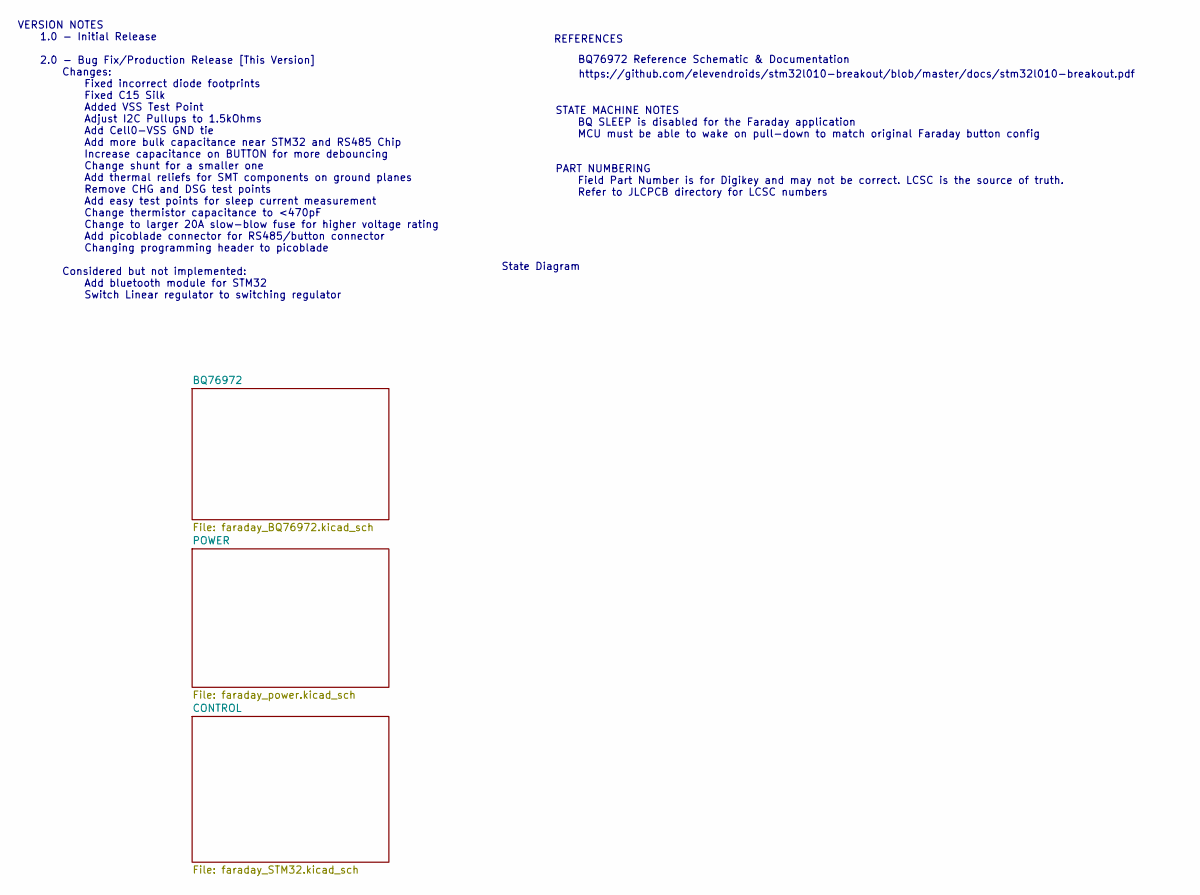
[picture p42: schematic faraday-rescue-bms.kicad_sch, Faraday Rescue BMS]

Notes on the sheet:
https://github.com/elevendroids/stm32l010-breakout/blob/master/docs/stm32l010-breakout.pdf
REFERENCES
BQ76972 Reference Schematic & Documentation
VERSION NOTES 1.0 - Initial Release 2.0 - Bug Fix/Production Release [This Version] Changes: Fixed incorrect diode footprints Fixed C15 Silk Added VSS Test Point Adjust I2C Pullups to 1.5kOhms Add Cell0-VSS GND tie Add more bulk capacitance near STM32 and RS485 Chip Increase capacitance on BUTTON f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
State Diagram
STATE MACHINE NOTES BQ SLEEP is disabled for the Faraday application MCU must be able to wake on pull-down to match original Faraday button config
PART NUMBERING Field Part Number is for Digikey and may not be correct. LCSC is the source of truth. Refer to JLCPCB directory for LCSC numbers

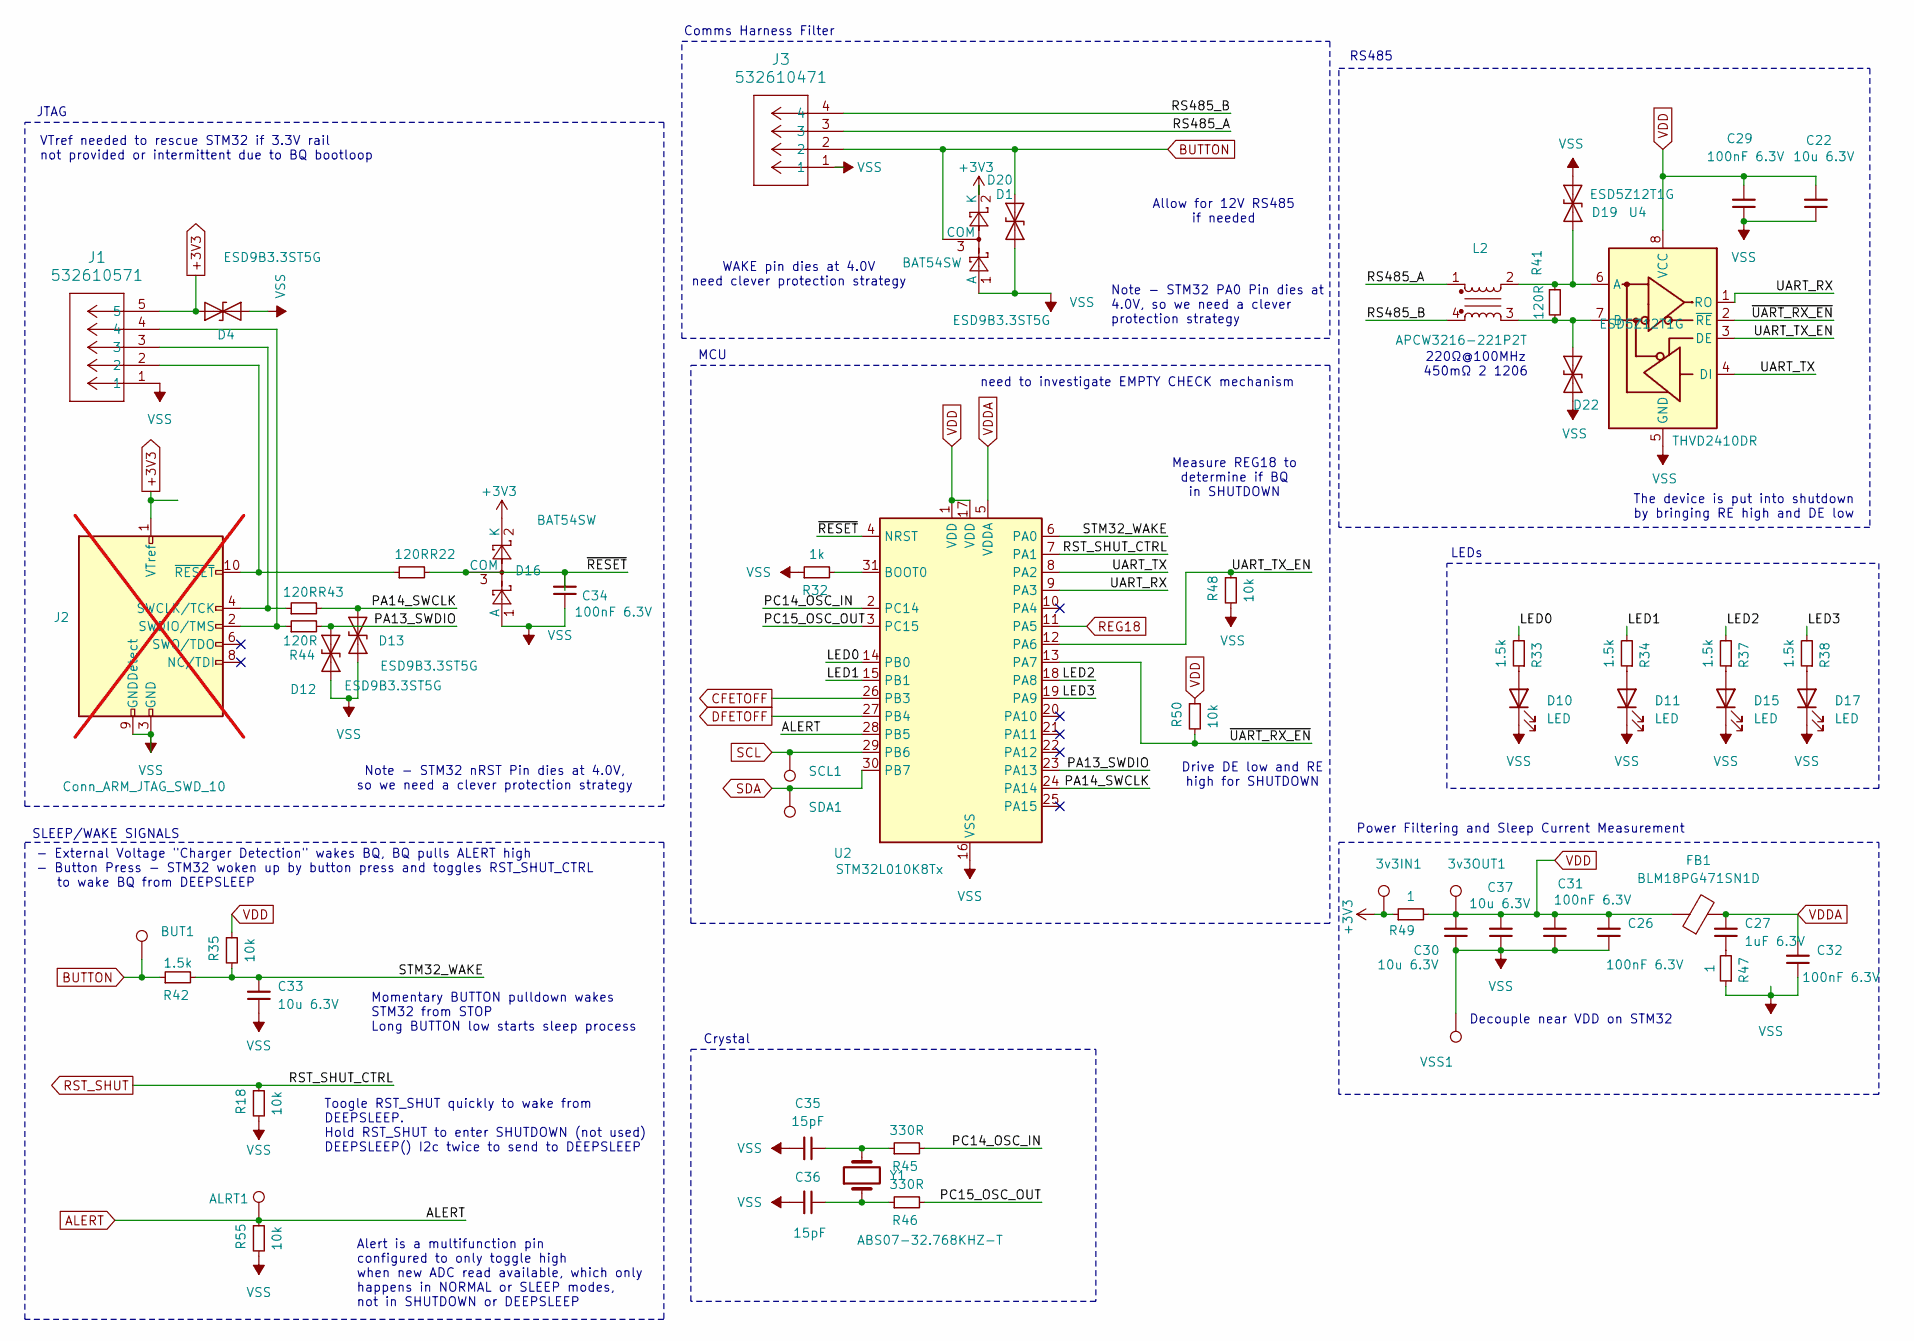
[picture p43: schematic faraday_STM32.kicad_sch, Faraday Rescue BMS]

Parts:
3v3IN1, 3v3OUT1: TestPoint_Keystone_5019_Minature; Part Number 36-5019CT-ND
ALRT1: TestPoint_Keystone_5019_Minature; Part Number 36-5019CT-ND
BUT1: TestPoint_Keystone_5019_Minature; Part Number 36-5019CT-ND
C22, C30, C37: 10u 6.3V; C_0402_1005Metric; Part Number CL05A106MP5NUNC
C26, C29, C31, C32, C34: 100nF 6.3V; C_0402_1005Metric; Part Number CC0402KRX7R7BB104
C27: 1uF 6.3V; C_0402_1005Metric; Part Number GRT155R61C105KE01D
C33: 10u 6.3V; C_0402_1005Metric; Part Number CC0402KRX7R7BB104
C35, C36: 15pF; C_0402_1005Metric; Part Number GJM1555C1H150GB01D
D1, D16: BAT54SW; SOT-323_SC-70; Part Number BAT54SW
D4, D12, D13, D20: ESD9B3.3ST5G; D_SOD-923; Part Number ESD9B3.3ST5G
D10, D11, D15, D17: LED; LED_0402_1005Metric; Part Number VLMO1500-GS08
D19, D22: ESD5Z12T1G; D_SOD-523; Part Number ESD5Z12T1G
FB1: BLM18PG471SN1D; L_0603_1608Metric; Part Number BLM18PG471SN1D
J1: 532610571; CONN_532610001-SD_05_MOL
J2: Conn_ARM_JTAG_SWD_10; PinHeader_2x05_P1.27mm_Vertical_SMD; Part Number 1156861; not fitted
J3: 532610471; CONN_532610001-SD_04_MOL
L2: APCW3216-221P2T; L_CommonMode_Wurth_WE-CNSW-1206; Part Number WCM3216F2SF-261T03
R18, R35, R48, R50, R55: 10k; R_0402_1005Metric; Part Number RC0402JR-0710KL
R22, R41, R43, R44: 120R; R_0402_1005Metric; Part Number RC0402JR-07120RL
R32: 1k; R_0402_1005Metric; Part Number RC0402JR-0710KL
R33, R34, R37, R38: 1.5k; R_0402_1005Metric; Part Number RC0402FR-07330RL
R42: 1.5k; R_0402_1005Metric; Part Number RC0402JR-07120RL
R45, R46: 330R; R_0402_1005Metric; Part Number RC1005J000CS
R47: 1; R_0402_1005Metric; Part Number RC0402JR-0710KL
R49: 1; R_0402_1005Metric; Part Number RC0402FR-071RL
SCL1: TestPoint_Keystone_5019_Minature; Part Number 36-5019CT-ND
SDA1: TestPoint_Keystone_5019_Minature; Part Number 36-5019CT-ND
U2: STM32L010K8Tx; LQFP-32_7x7mm_P0.8mm; Part Number STM32L010K8T6TR
U4: THVD2410DR; SOIC-8_3.9x4.9mm_P1.27mm; Part Number THVD2410DR
VSS1: TestPoint_Keystone_5019_Minature; Part Number 36-5019CT-ND
Y1: ABS07-32.768KHZ-T; R_1206_3216Metric; Part Number ABS07-32.768KHZ-T

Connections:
+3V3: 3v3IN1.1, D1.2 (K), D4.1 (A1), D16.2 (K), J1.5, J2.1 (VTref), R49.1; also elsewhere on the board
/CONTROL/LED0: R33.2, U2.14 (PB0)
/CONTROL/LED1: R34.2, U2.15 (PB1)
/CONTROL/LED2: R37.2, U2.18 (PA8)
/CONTROL/LED3: R38.2, U2.19 (PA9)
/CONTROL/PA13_SWDIO: D12.2 (A2), R44.2, U2.23 (PA13)
/CONTROL/PA14_SWCLK: D13.2 (A2), R43.2, U2.24 (PA14)
/CONTROL/PC14_OSC_IN: R45.2, U2.2 (PC14)
/CONTROL/PC15_OSC_OUT: R46.2, U2.3 (PC15)
/CONTROL/RS485_A: J3.3, L2.1
/CONTROL/RS485_B: J3.4, L2.4
/CONTROL/STM32_WAKE: C33.2, R35.2, R42.2, U2.6 (PA0)
/CONTROL/UART_RX: U2.9 (PA3), U4.1 (RO)
/CONTROL/UART_TX: U2.8 (PA2), U4.4 (DI)
/CONTROL/UART_TX_EN: R48.1, U2.12 (PA6), U4.3 (DE)
/CONTROL/~RESET: C34.2, D16.3 (COM), R22.2, U2.4 (NRST)
/CONTROL/~UART_RX_EN: R50.2, U2.13 (PA7), U4.2 (~RE)
ALERT: ALRT1.1, R55.1, U2.28 (PB5); also elsewhere on the board
BUTTON: BUT1.1, D1.3 (COM), D20.2 (A2), J3.2, R42.1
CFETOFF: U2.26 (PB3); also elsewhere on the board
DFETOFF: U2.27 (PB4); also elsewhere on the board
unnamed 37: J1.7, J3.6; also elsewhere on the board
unnamed: C27.1, R47.2
unnamed: C35.1, R45.1, Y1.2
unnamed: C36.1, R46.1, Y1.1
unnamed: D10.2 (A), R33.1
unnamed: D11.2 (A), R34.1
unnamed: D15.2 (A), R37.1
unnamed: D17.2 (A), R38.1
unnamed: D19.1 (A1), L2.2, R41.1, U4.6 (A)
unnamed: D22.1 (A1), L2.3, R41.2, U4.7 (B)
unnamed: J1.2, J2.10 (~RESET), R22.1
unnamed: J1.3, J2.4 (SWCLK/TCK), R43.1
unnamed: J1.4, J2.2 (SWDIO/TMS), R44.1
unnamed: R32.2, U2.31 (BOOT0)
REG18: U2.11 (PA5); also elsewhere on the board
RST_SHUT: R18.1, U2.7 (PA1); also elsewhere on the board
SCL: SCL1.1, U2.29 (PB6); also elsewhere on the board
SDA: SDA1.1, U2.30 (PB7); also elsewhere on the board
VDD: 3v3OUT1.1, C22.2, C26.2, C29.2, C30.2, C31.2, C37.2, FB1.1, R35.1, R49.2, R50.1, U2.1 (VDD), U2.17 (VDD), U4.8 (VCC)
VDDA: C27.2, C32.2, FB1.2, U2.5 (VDDA)
VSS: C22.1, C26.1, C29.1, C30.1, C31.1, C32.1, C33.1, C34.1, C35.2, C36.2, C37.1, D1.1 (A), D4.2 (A2), D10.1 (K), D11.1 (K), D12.1 (A1), D13.1 (A1), D15.1 (K), D16.1 (A), D17.1 (K), D19.2 (A2), D20.1 (A1), D22.2 (A2), J1.1, J1.6, J2.3 (GND), J2.5 (GND), J2.9 (GNDDetect), J3.1, J3.5, R18.2, R32.1, R47.1, R48.2, R55.2, U2.16 (VSS), U2.32 (VSS), U4.5 (GND), VSS1.1; also elsewhere on the board

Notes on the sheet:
220Ω@100MHz 450mΩ 2 1206
Decouple near VDD on STM32
Alert is a multifunction pin configured to only toggle high when new ADC read available, which only happens in NORMAL or SLEEP modes, not in SHUTDOWN or DEEPSLEEP
MCU
Note - STM32 PA0 Pin dies at 4.0V, so we need a clever protection strategy
RS485
WAKE pin dies at 4.0V need clever protection strategy
JTAG
Drive DE low and RE high for SHUTDOWN
- External Voltage "Charger Detection" wakes BQ, BQ pulls ALERT high - Button Press - STM32 woken up by button press and toggles RST_SHUT_CTRL to wake BQ from DEEPSLEEP
VTref needed to rescue STM32 if 3.3V rail not provided or intermittent due to BQ bootloop
Allow for 12V RS485 if needed
Momentary BUTTON pulldown wakes STM32 from STOP Long BUTTON low starts sleep process
SLEEP/WAKE SIGNALS
need to investigate EMPTY CHECK mechanism
Power Filtering and Sleep Current Measurement
Comms Harness Filter
Measure REG18 to determine if BQ in SHUTDOWN
The device is put into shutdown by bringing RE high and DE low
Toogle RST_SHUT quickly to wake from DEEPSLEEP. Hold RST_SHUT to enter SHUTDOWN (not used) DEEPSLEEP() I2c twice to send to DEEPSLEEP
Crystal
Note - STM32 nRST Pin dies at 4.0V, so we need a clever protection strategy
LEDs

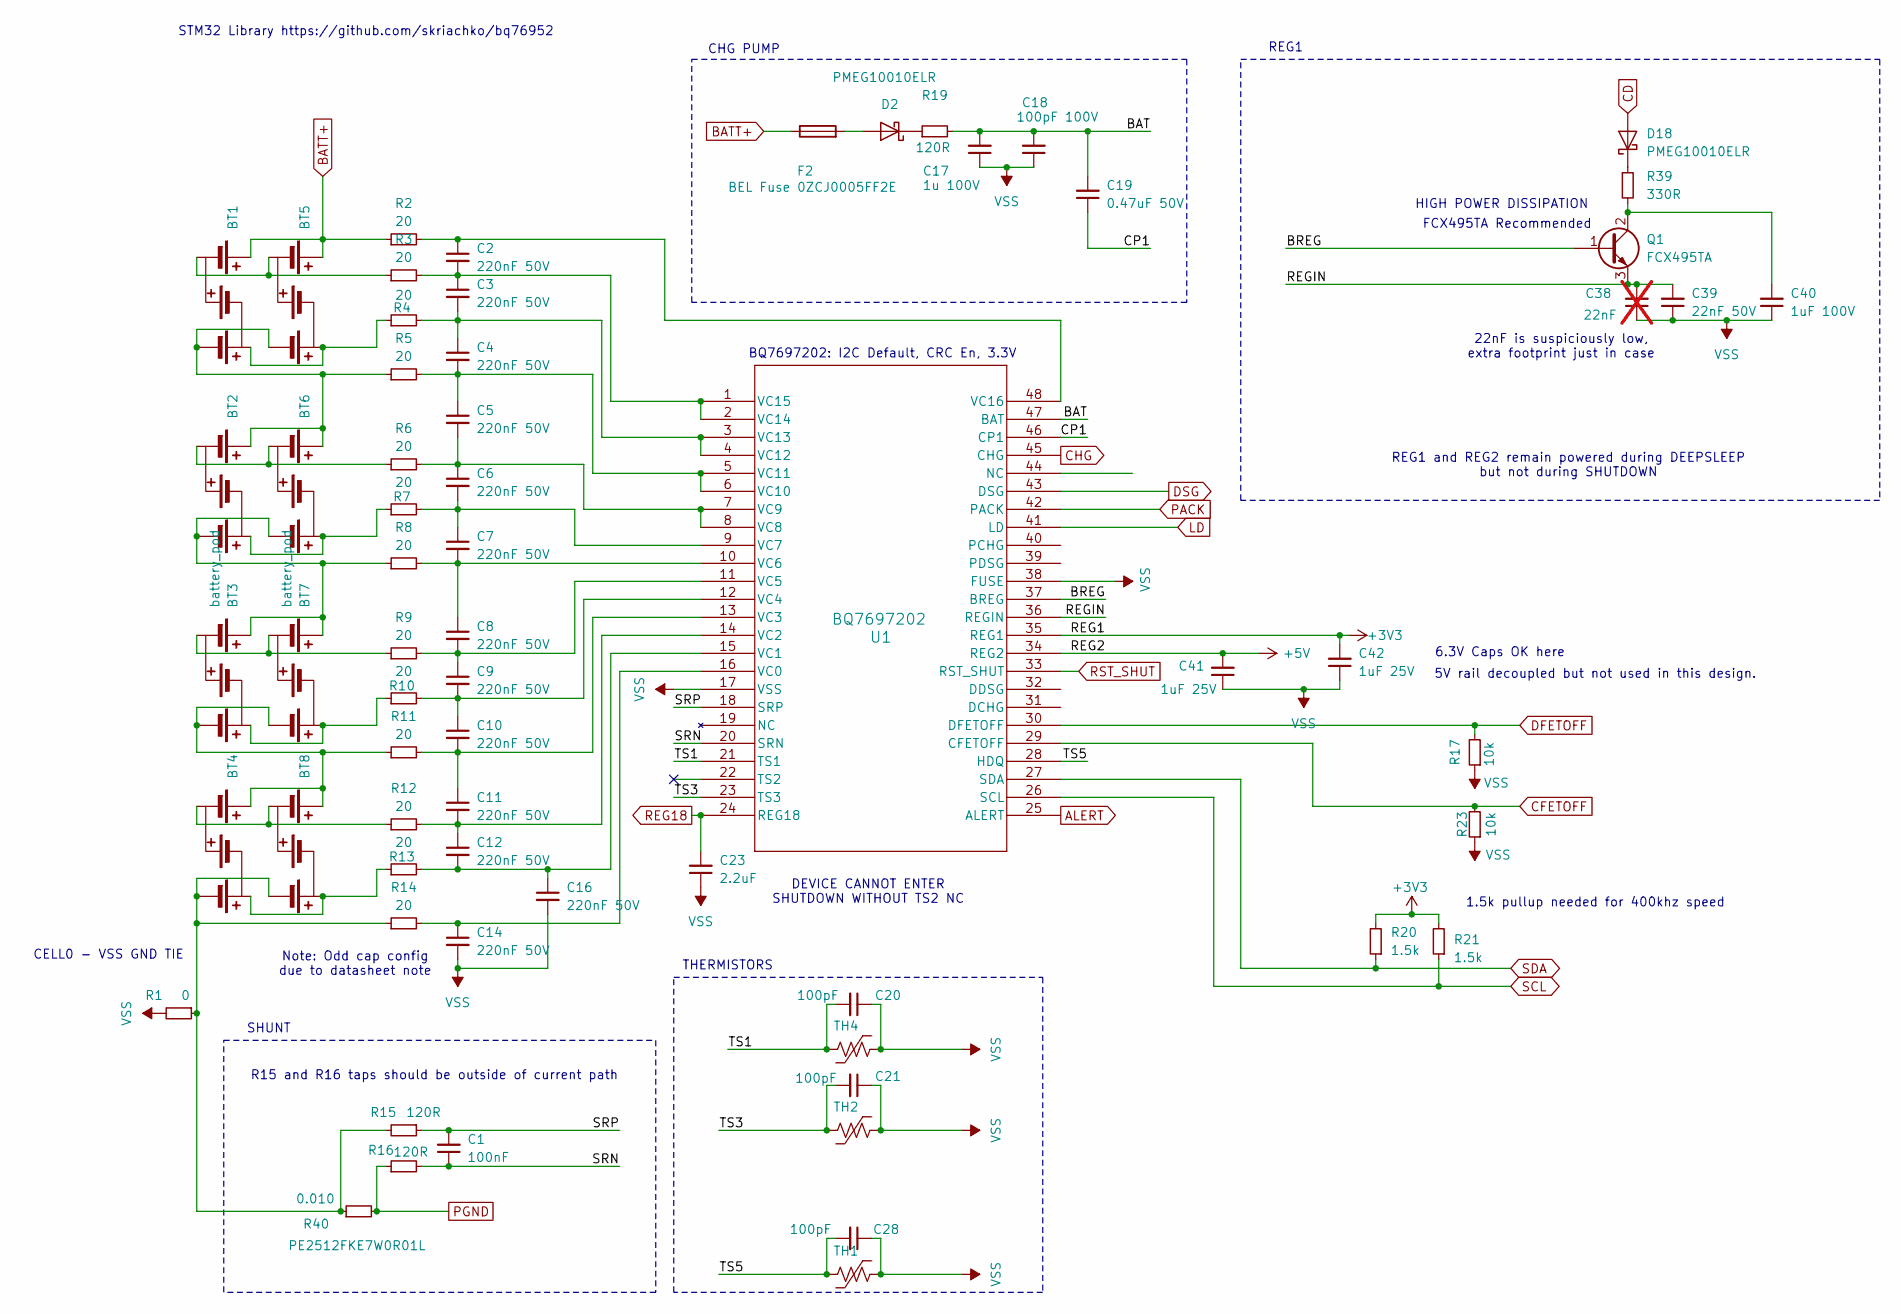
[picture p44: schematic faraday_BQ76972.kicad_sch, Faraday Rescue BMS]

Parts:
BT1, BT2, BT3, BT4, BT5, BT6, BT7, BT8: battery_pod; 3S 18650 Group
C1: 100nF; C_0402_1005Metric; Part Number CC0402KRX7R7BB104
C2, C3, C4, C5, C6, C7, C8, C9, C10, C11, C12, C14, C16: 220nF 50V; C_0402_1005Metric; Part Number GRM155R61H224KE01W
C17: 1u 100V; C_0805_2012Metric; Part Number CL21Y105KCYVPNE
C18: 100pF 100V; C_0805_2012Metric; Part Number CL21C101JC61PNC
C19: 0.47uF 50V; C_0805_2012Metric; Part Number CC0805KKX7R0BB474
C20, C21, C28: 100pF; C_0402_1005Metric; Part Number CC0402KRX7R7BB104
C23: 2.2uF; C_0402_1005Metric; Part Number CC0402KRX5R7BB225
C38: 22nF; C_0402_1005Metric; Part Number GRM155R71H223KA12D; not fitted
C39: 22nF 50V; C_0402_1005Metric; Part Number GRM155R71H223KA12D
C40: 1uF 100V; C_0805_2012Metric; Part Number CL21Y105KCYVPNE
C41, C42: 1uF 25V; C_0402_1005Metric; Part Number GRT155R61C105KE01D
D2, D18: PMEG10010ELR; Nexperia_CFP3_SOD-123W; Part Number PMEG10010ELR-QX
F2: BEL Fuse 0ZCJ0005FF2E; Fuse_1206_3216Metric; Part Number 0ZCJ0005FF2E
Q1: FCX495TA; SOT-89-3; Part Number FCX495TA
R1: 0; R_0402_1005Metric; Part Number RC0402JR-07120RL
R2, R3, R4, R5, R6, R7, R8, R9, R10, R11, R12, R13, R14: 20; R_1206_3216Metric; Part Number ESR18EZPF20R0
R15, R16: 120R; R_0402_1005Metric; Part Number RC0402JR-07120RL
R17, R23: 10k; R_0402_1005Metric; Part Number RC0402JR-0710KL
R19: 120R; R_1206_3216Metric; Part Number RC0402JR-07120RL
R20, R21: 1.5k; R_0402_1005Metric; Part Number RC0402JR-0710KL
R39: 330R; R_1206_3216Metric; Part Number RC0402FR-07330RL
R40: 0.010; R_2512_6332Metric; Part Number PE2512FKE7W0R01L
TH1, TH2: Thermistor_US; R_0402_1005Metric; Part Number NT04104F3435B1F
TH4: Thermistor_US; R_0402_1005Metric; Part Number CMFX 103F3435
U1: BQ7697202; TQFP48_PFB_TEX; Part Number BQ7697202PFBR

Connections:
+3V3: C42.2, R20.2, R21.2, U1.35 (REG1); also elsewhere on the board
+5V: C41.2, U1.34 (REG2)
/BQ76972/BAT: C17.2, C18.2, C19.2, R19.2, U1.47 (BAT)
/BQ76972/BREG: Q1.1 (B), U1.37 (BREG)
/BQ76972/CP1: C19.1, U1.46 (CP1)
/BQ76972/REGIN: C38.2, C39.2, Q1.3 (E), U1.36 (REGIN)
/BQ76972/SRN: C1.1, R16.2, U1.20 (SRN)
/BQ76972/SRP: C1.2, R15.1, U1.18 (SRP)
/BQ76972/TS1: C20.2, TH4.1, U1.21 (TS1)
/BQ76972/TS3: C21.2, TH2.1, U1.23 (TS3)
/BQ76972/TS5: C28.2, TH1.1, U1.28 (HDQ)
ALERT: U1.25 (ALERT); also elsewhere on the board
BATT+: BT1.1 (+), BT5.1 (+), F2.1, R2.1; also elsewhere on the board
CD: D18.2 (A); also elsewhere on the board
CFETOFF: R23.2, U1.29 (CFETOFF); also elsewhere on the board
CHG: U1.45 (CHG); also elsewhere on the board
DFETOFF: R17.2, U1.30 (DFETOFF); also elsewhere on the board
DSG: U1.43 (DSG); also elsewhere on the board
LD: U1.41 (LD); also elsewhere on the board
unnamed 37: BT1.3 (+), BT5.3 (+), R4.1; also elsewhere on the board
unnamed: BT1.2 (-), BT5.2 (-), R3.1
unnamed: BT1.4 (-), BT2.1 (+), BT5.4 (-), BT6.1 (+), R5.1
unnamed: BT2.3 (+), BT6.3 (+), R7.1
unnamed: BT2.2 (-), BT6.2 (-), R6.1
unnamed: BT2.4 (-), BT3.1 (+), BT6.4 (-), BT7.1 (+), R8.1
unnamed: BT3.3 (+), BT7.3 (+), R10.1
unnamed: BT3.2 (-), BT7.2 (-), R9.1
unnamed: BT3.4 (-), BT4.1 (+), BT7.4 (-), BT8.1 (+), R11.1
unnamed: BT4.3 (+), BT8.3 (+), R13.1
unnamed: BT4.2 (-), BT8.2 (-), R12.1
unnamed: BT4.4 (-), BT8.4 (-), R1.1, R14.1, R15.2, R40.1
unnamed: D2.2 (A), F2.2
unnamed: D2.1 (K), R19.1
unnamed: D18.1 (K), R39.1
unnamed: C40.2, Q1.2 (C), R39.2
unnamed: C14.1, R14.2, U1.16 (VC0)
unnamed: C12.2, C16.1, R13.2, U1.15 (VC1)
unnamed: C11.2, C12.1, R12.2, U1.14 (VC2)
unnamed: C10.2, C11.1, R11.2, U1.13 (VC3)
unnamed: C9.2, C10.1, R10.2, U1.12 (VC4)
unnamed: C8.2, C9.1, R9.2, U1.11 (VC5)
unnamed: C7.2, C8.1, R8.2, U1.10 (VC6)
unnamed: C6.2, C7.1, R7.2, U1.9 (VC7)
unnamed: C5.2, C6.1, R6.2, U1.7 (VC9), U1.8 (VC8)
unnamed: C4.2, C5.1, R5.2, U1.5 (VC11), U1.6 (VC10)
unnamed: C3.2, C4.1, R4.2, U1.3 (VC13), U1.4 (VC12)
unnamed: C2.2, C3.1, R3.2, U1.1 (VC15), U1.2 (VC14)
unnamed: C2.1, R2.2, U1.48 (VC16)
PACK: U1.42 (PACK); also elsewhere on the board
PGND: R16.1, R40.2; also elsewhere on the board
REG18: C23.2, U1.24 (REG18); also elsewhere on the board
RST_SHUT: U1.33 (RST_SHUT); also elsewhere on the board
SCL: R21.1, U1.26 (SCL); also elsewhere on the board
SDA: R20.1, U1.27 (SDA); also elsewhere on the board
VSS: C14.2, C16.2, C17.1, C18.1, C20.1, C21.1, C23.1, C28.1, C38.1, C39.1, C40.1, C41.1, C42.1, R1.2, R17.1, R23.1, TH1.2, TH2.2, TH4.2, U1.17 (VSS), U1.38 (FUSE); also elsewhere on the board

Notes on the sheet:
BQ7697202: I2C Default, CRC En, 3.3V
CELL0 - VSS GND TIE
STM32 Library https://github.com/skriachko/bq76952
REG1
CHG PUMP
5V rail decoupled but not used in this design.
R15 and R16 taps should be outside of current path
Note: Odd cap config due to datasheet note
22nF is suspiciously low, extra footprint just in case
REG1 and REG2 remain powered during DEEPSLEEP but not during SHUTDOWN
THERMISTORS
SHUNT
DEVICE CANNOT ENTER SHUTDOWN WITHOUT TS2 NC
6.3V Caps OK here
1.5k pullup needed for 400khz speed
FCX495TA Recommended
HIGH POWER DISSIPATION

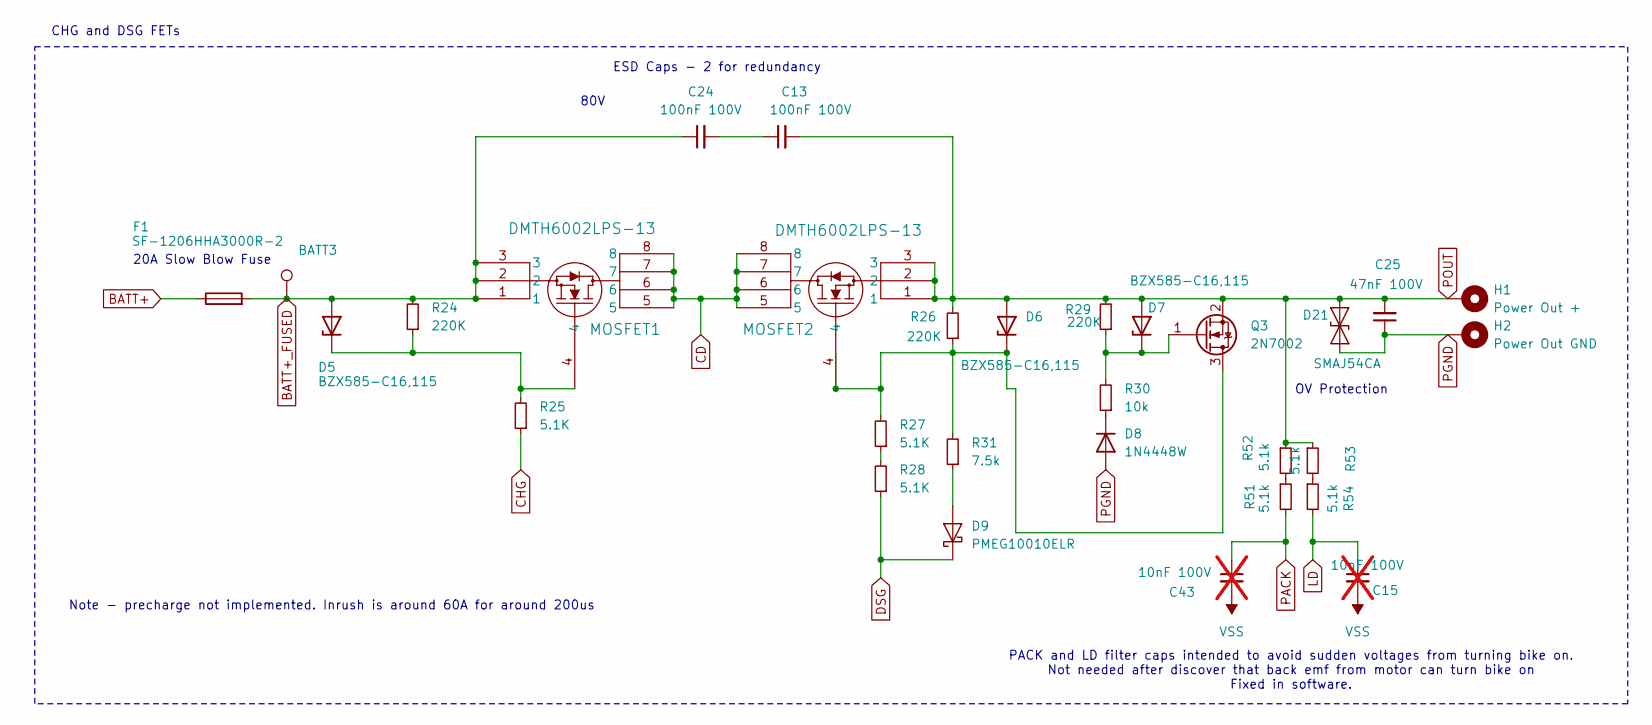
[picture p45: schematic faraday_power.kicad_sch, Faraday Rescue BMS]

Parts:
BATT3: TestPoint_Keystone_5019_Minature; Part Number 36-5019CT-ND
C13, C24: 100nF 100V; C_0603_1608Metric; Part Number CL10B104KC8NNNC
C15, C43: 10nF 100V; C_0805_2012Metric; Part Number CGA4J2X7R2A473K125AA; not fitted
C25: 47nF 100V; C_0805_2012Metric; Part Number CGA4J2X7R2A473K125AA
D5, D6, D7: BZX585-C16,115; D_SOD-523; Part Number BZX585-C16,115
D8: 1N4448W; D_SOD-123; Part Number 1N4448W
D9: PMEG10010ELR; Nexperia_CFP3_SOD-123W; Part Number PMEG10010ELR-QX
D21: SMAJ54CA; D_SMA; Part Number SMAJ54CA
F1: SF-1206HHA3000R-2; R_1206_3216Metric; Part Number SF-1206HHA3000R-2
H1: Power Out +; MountingHole_2.5mm_Pad_Via
H2: Power Out GND; MountingHole_2.5mm_Pad_Via
MOSFET1, MOSFET2: DMTH6002LPS-13; POWERDI5060-8_K_DIO; Part Number DMTH6002LPS-13
Q3: 2N7002; SOT-23; Part Number 2N7002
R24, R26, R29: 220K; R_0402_1005Metric; Part Number RC0402FR-07220KL
R25, R27, R28: 5.1K; R_0402_1005Metric; Part Number RC0402FR-075K1L
R30: 10k; R_0402_1005Metric; Part Number RC0402JR-0710KL
R31: 7.5k; R_0402_1005Metric; Part Number RC0402FR-077K5L
R51, R52, R53, R54: 5.1k; R_0402_1005Metric; Part Number RC0402FR-075K1L

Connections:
BATT+: F1.1; also elsewhere on the board
BATT+_FUSED: BATT3.1, C24.1, D5.2 (A), F1.2, MOSFET1.1, MOSFET1.2, MOSFET1.3, R24.2
CD: MOSFET1.5, MOSFET1.6, MOSFET1.7, MOSFET1.8, MOSFET2.5, MOSFET2.6, MOSFET2.7, MOSFET2.8; also elsewhere on the board
CHG: R25.1; also elsewhere on the board
DSG: D9.1 (K), R28.1; also elsewhere on the board
LD: C15.1, R54.2; also elsewhere on the board
unnamed: C13.1, C24.2
unnamed: D5.1 (K), MOSFET1.4, R24.1, R25.2
unnamed: D6.1 (K), MOSFET2.4, Q3.3 (D), R26.1, R27.2, R31.2
unnamed: D7.1 (K), Q3.1 (G), R29.1, R30.2
unnamed: D8.1 (K), R30.1
unnamed: D9.2 (A), R31.1
unnamed: R27.1, R28.2
unnamed: R51.1, R52.2
unnamed: R53.2, R54.1
PACK: C43.1, R51.2; also elsewhere on the board
PGND: C25.1, D8.2 (A), D21.1 (A1), H2.1; also elsewhere on the board
POUT: C13.2, C25.2, D6.2 (A), D7.2 (A), D21.2 (A2), H1.1, MOSFET2.1, MOSFET2.2, MOSFET2.3, Q3.2 (S), R26.2, R29.2, R52.1, R53.1
VSS: C15.2, C43.2; also elsewhere on the board

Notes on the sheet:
ESD Caps - 2 for redundancy
20A Slow Blow Fuse
Note - precharge not implemented. Inrush is around 60A for around 200us
OV Protection
CHG and DSG FETs
80V
PACK and LD filter caps intended to avoid sudden voltages from turning bike on. Not needed after discover that back emf from motor can turn bike on Fixed in software.

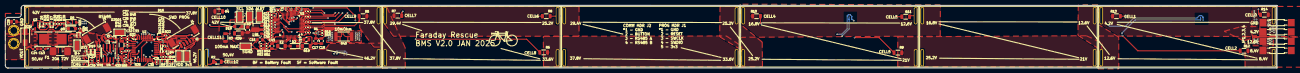
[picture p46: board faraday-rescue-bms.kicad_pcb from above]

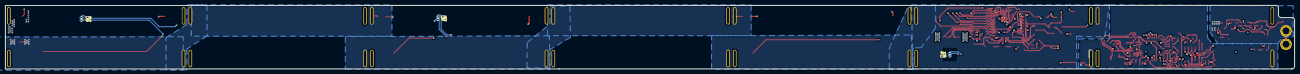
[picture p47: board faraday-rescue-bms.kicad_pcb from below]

Board: 4 copper layers, 481.3 x 23.7 mm, 151 parts (6 on the bottom side), 98 nets.

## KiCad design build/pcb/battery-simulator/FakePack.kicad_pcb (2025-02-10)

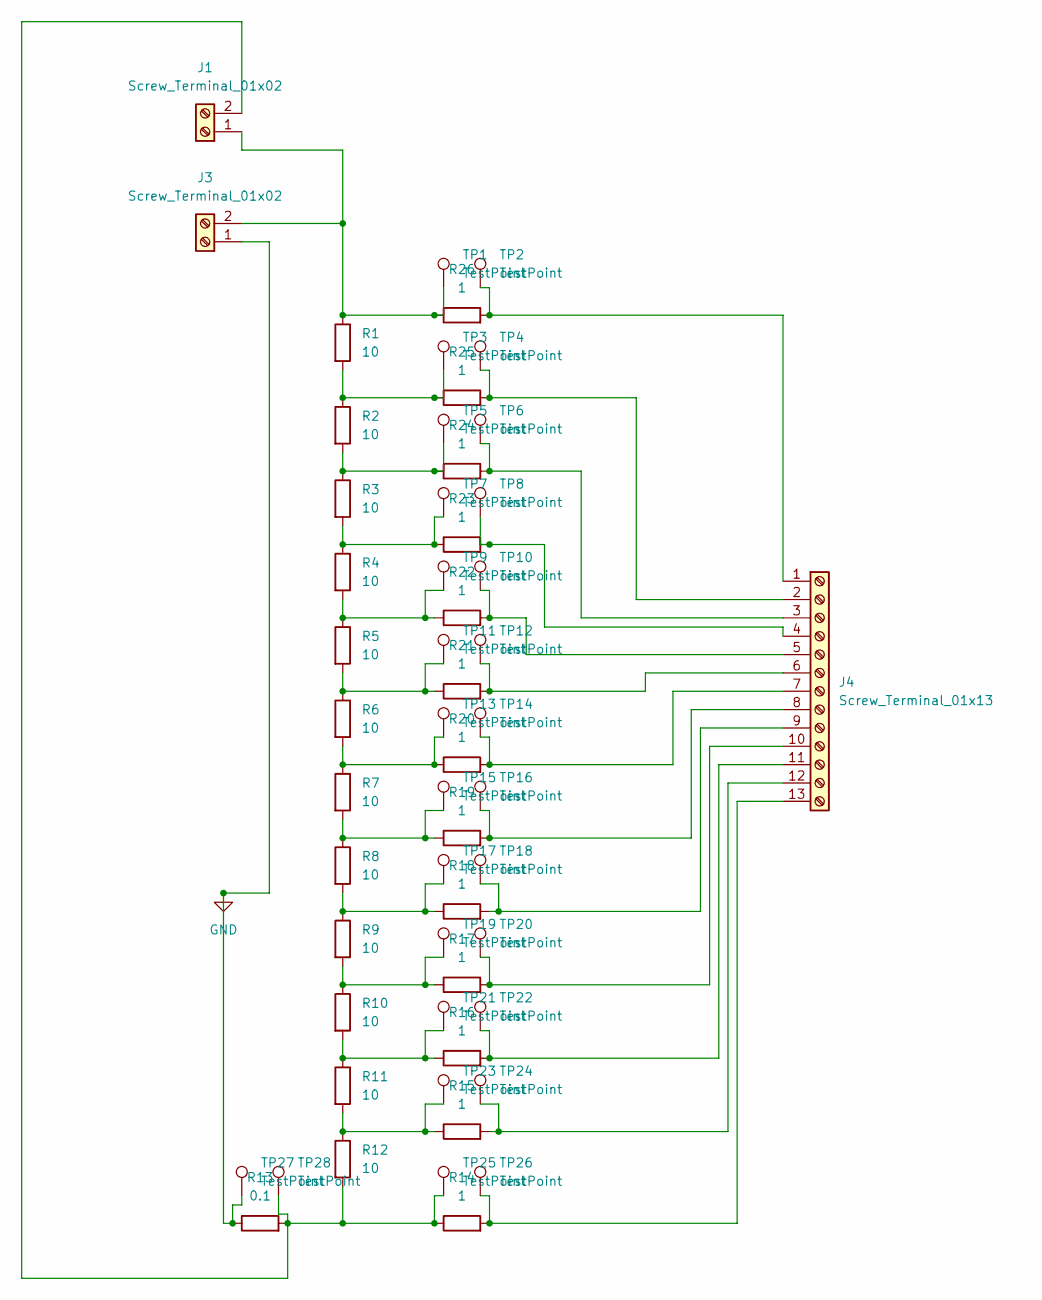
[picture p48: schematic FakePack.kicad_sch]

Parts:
J1, J3: Screw_Terminal_01x02; TerminalBlock_4Ucon_1x02_P3.50mm_Horizontal
J4: Screw_Terminal_01x13; TerminalBlock_Xinya_XY308-2.54-13P_1x13_P2.54mm_Horizontal
R1, R2, R3, R4, R5, R6, R7, R8, R9, R10, R11, R12: 10; R_Axial_DIN0918_L18.0mm_D9.0mm_P22.86mm_Horizontal
R13: 0.1; R_1206_3216Metric
R14, R15, R16, R17, R18, R19, R20, R21, R22, R23, R24, R25, R26: 1; R_0805_2012Metric
TP1, TP2, TP3, TP4, TP5, TP6, TP7, TP8, TP9, TP10, TP11, TP12, TP13, TP14, TP15, TP16, TP17, TP18, TP19, TP20, TP21, TP22, TP23, TP24, TP25, TP26, TP27, TP28: TestPoint; TestPoint_Keystone_5010-5014_Multipurpose

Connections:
GND: J3.1, R13.1, TP27.1; also elsewhere on the board
unnamed 1: J1.1, J3.2, R1.1, R26.1, TP1.1; also elsewhere on the board
unnamed: J4.1, R26.2, TP2.1
unnamed: J4.2, R25.2, TP4.1
unnamed: J4.3, R24.2, TP6.1
unnamed: J4.4, R23.2, TP8.1
unnamed: J4.5, R22.2, TP10.1
unnamed: J4.6, R21.2, TP12.1
unnamed: J4.7, R20.2, TP14.1
unnamed: J4.8, R19.2, TP16.1
unnamed: J4.9, R18.2, TP18.1
unnamed: J4.10, R17.2, TP20.1
unnamed: J4.11, R16.2, TP22.1
unnamed: J4.12, R15.2, TP24.1
unnamed: J4.13, R14.2, TP26.1
unnamed: R1.2, R2.1, R25.1, TP3.1
unnamed: R2.2, R3.1, R24.1, TP5.1
unnamed: R9.2, R10.1, R17.1, TP19.1
unnamed: R10.2, R11.1, R16.1, TP21.1
unnamed: R11.2, R12.1, R15.1, TP23.1
unnamed: J1.2, R12.2, R13.2, R14.1, TP25.1, TP28.1
unnamed: R8.2, R9.1, R18.1, TP17.1
unnamed: R7.2, R8.1, R19.1, TP15.1
unnamed: R6.2, R7.1, R20.1, TP13.1
unnamed: R5.2, R6.1, R21.1, TP11.1
unnamed: R4.2, R5.1, R22.1, TP9.1
unnamed: R3.2, R4.1, R23.1, TP7.1

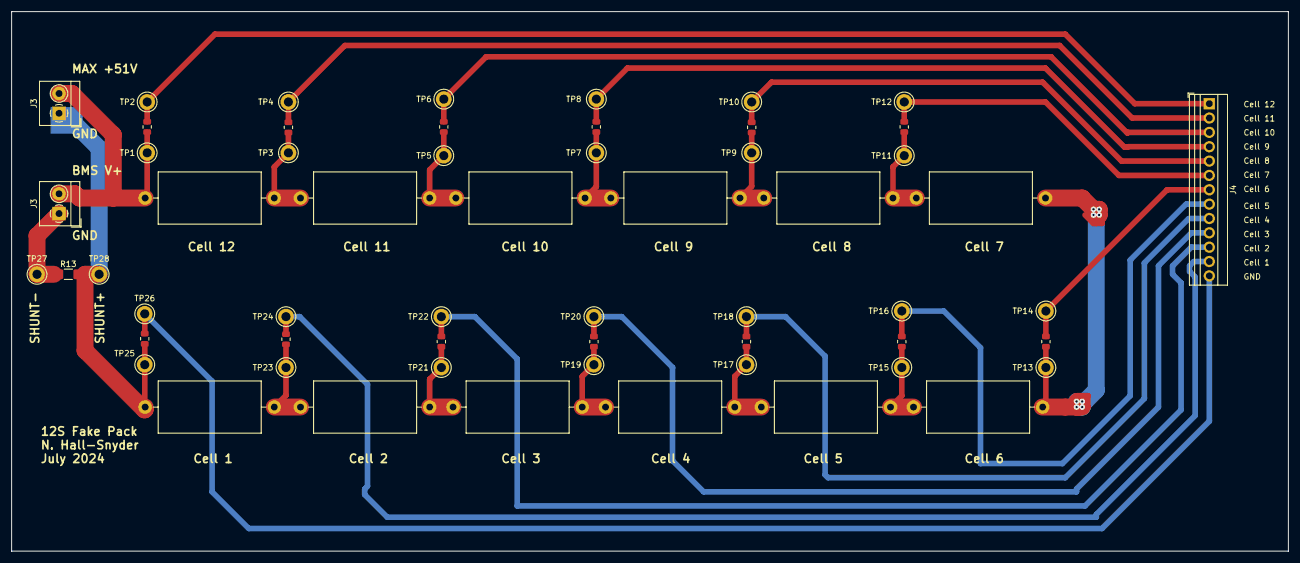
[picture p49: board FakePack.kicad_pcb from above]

Board: 2 copper layers, 226.0 x 95.5 mm, 57 parts (0 on the bottom side), 27 nets.

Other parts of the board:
J3#2: Screw_Terminal_01x02; TerminalBlock_4Ucon_1x02_P3.50mm_Horizontal

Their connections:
GND: J3#2.1; also elsewhere on the board
unnamed 1: J3#2.2; also elsewhere on the board

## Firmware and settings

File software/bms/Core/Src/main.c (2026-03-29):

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
/* Includes ------------------------------------------------------------------*/
#include "main.h"
#include "stdio.h"
#include "utils.h"
#include "BQ769x2.h"

ADC_HandleTypeDef hadc;

I2C_HandleTypeDef hi2c1;

TIM_HandleTypeDef htim2;

UART_HandleTypeDef huart2;

IWDG_HandleTypeDef hiwdg;

RTC_HandleTypeDef hrtc;

/* Program Options */
#define DEBUG 0 //Debug mode disables RS485 communications to the bike and instead enables debug messages over RS485, including printf.
#define LEDS 0 //Set to 1 to enable LEDs, 0 to disable. LEDs consume surprisingly large amounts of power because of the linear regulator from 48V to 3.3V
#define WATCHDOG 1 //set to 1 to enable watchdog. Good for production, bad for debugging
#define RESET_3V3 0 //set to 1 reset 3v3 rail. Useful if STM32 doesn't sleep after debugging with debugger.

/*Pin Definitions
 * --------------
 * Note - I2C Pin definitions and RS485 TX/RX definitions are handled in HAL init functions*/

//LED that indicates CHG state
#define LED_CHG_PORT GPIOB
#define LED_CHG_PIN GPIO_PIN_0

//LED that indicates DSG state
#define LED_DSG_PORT GPIOB
#define LED_DSG_PIN GPIO_PIN_1

//Active-high to veto charge FET
#define CFETOFF_PORT GPIOB
#define CFETOFF_PIN GPIO_PIN_3

//Active-high to veto discharge FET
#define DFETOFF_PORT GPIOB
#define DFETOFF_PIN GPIO_PIN_4

//Active-low on-button from faraday bike. Used in this file and stm32l0xx_it.c
#define BUTTON_PORT GPIOA
#define BUTTON_PIN GPIO_PIN_0

//RST_SHUT_CTRL used by STM to change BQ sleep states
#define RST_SHUT_PORT GPIOA
#define RST_SHUT_PIN GPIO_PIN_1

//REG18 analog value from BQ chip. Read to check if BQ is in SHUTDOWN
#define REG18_AIN_PORT GPIOA
#define REG18_AIN_PIN GPIO_PIN_5

//LED2 General Purpose
#define LED_BF_PORT GPIOA
#define LED_BF_PIN GPIO_PIN_8

//LED3 General Purpose
#define LED_SF_PORT GPIOA
#define LED_SF_PIN GPIO_PIN_9

//Alert configurable output from BQ chip. Not used in this file, set in stm32l0xx_it.c
#define ALERT_PORT GPIOB
#define ALERT_PIN GPIO_PIN_5

//UART_TX_EN - enable transmit on RS485 transceiver, active high
#define UART_TX_EN_PORT GPIOA
#define UART_TX_EN_PIN GPIO_PIN_6

//UART_RX_EN - enable receive on RS485 transceiver, active low
#define UART_RX_EN_PORT GPIOA
#define UART_RX_EN_PIN GPIO_PIN_7

/*BQ Chip Parameters*/
#define ACTIVE_CELLS 0xAAFF //bitfield which indicates which cells to have protections on. Specific to this Faraday 12S pack
#define BQ_DEV_ADDR  0x10 //i2c address
#define BQ_CRC_MODE 1  // 0 for disabled, 1 for enabled

/* User-Facing Timing Parameters */
#define RETRY_LIMIT 100 //number of times the STM will retry communications with BQ before calling for a hard reset
#define INACTIVITY_LOOPS_MAX 11000 //number of loops without significant battery current before bike goes into sleep. Normally around 5 minutes for 10,000 loops
#define BUTTON_LONG_PRESS_LOOPS 15 //number of loops that count as a long press
#define UART_TIMEOUT_S 3 //default timeout for RS485 in seconds
#define PACK_CURRENT_INACTIVITY_LOWER_LIMIT_MA -250
#define PACK_CURRENT_INACTIVITY_UPPER_LIMIT_MA 75

/*Uart Variables flag*/
__IO ITStatus UartBusy = RESET;

/* USER CODE BEGIN PV */

//Used for state machine
typedef struct {
	uint8_t ButtonCount;
	uint16_t CRC_Fail;
	uint16_t InactivityCount;
	uint16_t RetryCount;
	uint8_t ResetByWatchdog;
	uint8_t ButtonPressedDuringBoot;
} STM32State;

//Global Variables
STM32State state;
BQState batt;
uint8_t UART_RxData[8] = { 0x00, 0x00, 0x00, 0x00, 0x00, 0x00, 0x00, 0x00 };
uint8_t UART_TxData[32] = { 0x00, 0x00, 0x00, 0x00, 0x00, 0x00, 0x00, 0x00,
		0x00, 0x00, 0x00, 0x00, 0x00, 0x00, 0x00, 0x00, 0x00, 0x00, 0x00, 0x00,
		0x00, 0x00, 0x00, 0x00, 0x00, 0x00, 0x00, 0x00, 0x00, 0x00, 0x00, 0x00 };

/* USER CODE END PV */

static void SystemClock_Config(void);
static void SystemPower_Config(void);
static void MX_GPIO_Init(void);
static void MX_ADC_Init(void);
static void MX_I2C1_Init(void);
static void MX_USART2_UART_Init(void);
static void MX_TIM2_Init(void);
static void MX_IWDG_Init(void);
static void MX_RTC_Init(void);
static void EXTI0_1_IRQHandler_Config(void);
static void EXTI2_3_IRQHandler_Config(void);
static void THVD2410_Sleep();
static void THVD2410_Transmit();
static void THVD2410_Receive();
static uint8_t UART_PrepCellVoltageMessage();
static uint8_t UART_PrepCellBalancingMessage();
static uint8_t UART_PrepBatteryStatusMessage1();
static uint8_t UART_PrepBatteryStatusMessage2();
uint8_t STM32_Wake_Button_Pressed();
void Sleep();

#ifdef __GNUC__
/* With GCC, small printf (option LD Linker->Libraries->Small printf
 set to 'Yes') calls __io_putchar() */
#define PUTCHAR_PROTOTYPE int __io_putchar(int ch)
#else
#define PUTCHAR_PROTOTYPE int fputc(int ch, FILE *f)
#endif /* __GNUC__ */

/**
 * @brief  Retargets the C library printf function to the USART.
 * @param  None
 * @retval None
 */

/* USER CODE BEGIN PFP */

/* Helper Functions -----------------------------------------------*/
/* debug function to print lots of status bits */
void BQ769x2_PrintStatus(BQState *s) {
	s->AlarmBits = BQ769x2_ReadRawAlarmStatus(&batt);
	BQ769x2_ReadPFStatus(&batt); //TODO remove later
	BQ769x2_CalcMinMaxCellV(&batt);
	printf(
			"CRC: %d Bal: %d Dsg: %d Chg: %d ScanComplete: %d Prots: %d SSA: %d SSBC: %d PFA: %d PFB: %d PFC: %d UV: %d OV: %d SCD: %d OCD: %d SSA: %#x, SSB: %#x, SSC: %#x",
			batt.CRC_Fail,
			//batt.AlarmBits & 0x00 ? 1 : 0, //WAKE
			//batt.AlarmBits & 0x02 ? 1 : 0, //ADSCAN
			batt.AlarmBits & 0x04 ? 1 : 0, //CB
			//batt.AlarmBits & 0x10 ? 1 : 0, //SHUTV
			batt.AlarmBits & 0x20 ? 0 : 1, //XDSG
			batt.AlarmBits & 0x40 ? 0 : 1, //XCHG
			batt.AlarmBits & 0x80 ? 1 : 0, //FULLSCAN
			//batt.AlarmBits & 0x200 ? 1 : 0, //INITCOMP
			//batt.AlarmBits & 0x400 ? 1 : 0, //INITSTART
			batt.ProtectionsTriggered, batt.AlarmBits & 0x4000 ? 1 : 0, //Safety Status A
			batt.AlarmBits & 0x8000 ? 1 : 0, //Safety Status B or C
			batt.value_PFStatusA, batt.value_PFStatusB, batt.value_PFStatusC,
			batt.UV_Fault, batt.OV_Fault, batt.SCD_Fault, batt.OCD_Fault,
			batt.value_SafetyStatusA, batt.value_SafetyStatusB,
			batt.value_SafetyStatusC);

	printf(
			"PackV: %d StackV:%d LdV:%d I: %d MIN_V: %d MAX_V: %d InactivityCount: %d TS1: %.3f TS3: %.3f T_HDQ: %.3f T_INT: %.3f \r\n",
			batt.Pack_Voltage, batt.Stack_Voltage, batt.LD_Voltage,
			batt.Pack_Current, batt.CellMinV, batt.CellMaxV,
			state.InactivityCount, batt.Temperature[0], batt.Temperature[1],
			batt.Temperature[2], batt.Temperature[3]);

}

/* UART Functions
 * ===================== */
//calculate faraday modbus CRC
uint16_t UART_CRC(uint8_t *buf, uint16_t size) {
	uint16_t crc = 0xFFFF;

	uint8_t n;
	uint8_t i;
	for (n = 0; n < size; n++) {
		crc = crc ^ buf[n];
		for (i = 0; i < 8; i++) {
			if (crc & 1) {
				crc = crc >> 1;
				crc = crc ^ 0xA001;
			} else {
				crc = crc >> 1;
			}
		}
	}
	return crc;
}

void THVD2410_Sleep() {
	HAL_GPIO_WritePin(UART_TX_EN_PORT, UART_TX_EN_PIN, GPIO_PIN_RESET);
	HAL_GPIO_WritePin(UART_RX_EN_PORT, UART_RX_EN_PIN, GPIO_PIN_SET);
}
;
void THVD2410_Transmit() {
	HAL_GPIO_WritePin(UART_TX_EN_PORT, UART_TX_EN_PIN, GPIO_PIN_SET);
	HAL_GPIO_WritePin(UART_RX_EN_PORT, UART_RX_EN_PIN, GPIO_PIN_SET);
}
;
void THVD2410_Receive() {
	HAL_GPIO_WritePin(UART_TX_EN_PORT, UART_TX_EN_PIN, GPIO_PIN_RESET);
	HAL_GPIO_WritePin(UART_RX_EN_PORT, UART_RX_EN_PIN, GPIO_PIN_RESET);
}
;

/* interrupt-safe function to clear RxData and wait for a new message */
void UART_WaitForCommand() {

	if (!UartBusy) {
		//set RX buffer to all zeros
		for (int i = 0; i < 8; i++) {
			UART_RxData[i] = 0;
		}

		//set transciever to receive
		THVD2410_Receive();

		//start recieve-to-idle interrupt
		huart2.RxState = HAL_UART_STATE_READY;
		if (HAL_UARTEx_ReceiveToIdle_IT(&huart2, UART_RxData, 8) != HAL_OK) {
			Error_Handler();
		}
	}

}

/*
 * Prep cell balancing message (30 bytes). Refer to documentation for packet format
 */
uint8_t UART_PrepCellVoltageMessage() {

	for (int i = 0; i < 32; i++) {
		UART_TxData[i] = 0;
	}

	//device, fxn, length
	UART_TxData[0] = 0x02;
	UART_TxData[1] = 0x03;
	UART_TxData[2] = 0x18;

	// loop through voltage field and construct uints
	int k = 0;
	for (int i = 0; i < 16; i++) {
		if (batt.ActiveCells & (1 << i)) {
			UART_TxData[2 * k + 3] = (batt.CellVoltage[i] * 2 / 3) >> 8;
			UART_TxData[2 * k + 4] = (batt.CellVoltage[i] * 2 / 3) & 0xFF;

			//UART_TxData[2 * k + 3] = (3100 * 2 / 3) >> 8;
			//UART_TxData[2 * k + 4] = (3100 * 2 / 3) & 0xFF;
			k++;
		}
	}

	//add crc in reverse byte order
	uint16_t crc = UART_CRC(UART_TxData, 27);
	UART_TxData[27] = crc & 0xFF;
	UART_TxData[28] = crc >> 8;
	UART_TxData[29] = 0xFF; //add extra byte of zeros to match faraday protocol

	return 30;
}

/*
 * Prep cell balancing message (8 bytes). Refer to documentation for packet format
 */
uint8_t UART_PrepCellBalancingMessage() {

	for (int i = 0; i < 32; i++) {
		UART_TxData[i] = 0;
	}

	UART_TxData[0] = 0x02;
	UART_TxData[1] = 0x03;
	UART_TxData[2] = 0x02;

	// CB_ActiveCells is a bitfield of which of 16 channels are active. Bike expects a bitfield with the first byte blank and the remainder a bitfield
	uint16_t CB = 0x00;
	int k = 0;
	for (int i = 0; i < 16; i++) {
		if (batt.ActiveCells & (1 << i)) {
			//i is the cell number active cell bitfield (0xAAFF)
			//k is the cell number in faraday index
			if (batt.CB_ActiveCells & (1 << i)) {
				CB = CB | (1 << k); //TODO determine whether the cell number is mapped correctly
			};
			k++;
		}
	}

	UART_TxData[3] = CB >> 8;
	UART_TxData[4] = CB & 0xFF;

	//add crc in reverse byte order
	uint16_t crc = UART_CRC(UART_TxData, 5);
	UART_TxData[5] = crc & 0xFF;
	UART_TxData[6] = crc >> 8;
	UART_TxData[7] = 0xFF; //add extra byte of zeros to match faraday protocol
	return 8;
}

/*
 * Prep battery status 1 message (8 bytes). Refer to documentation for packet format
 * Respond to battery status message 1 - battery OK.
 *
 * Hard coded for now
 * Example request 0x2 0x3 0x0 0x0 0x0 0x1 0x84 0x39
 * Example response 0x2 0x3 0x2 0x0 0x0 0xfc 0x44
 */
uint8_t UART_PrepBatteryStatusMessage1() {

	for (int i = 0; i < 32; i++) {
		UART_TxData[i] = 0;
	}

	UART_TxData[0] = 0x02;
	UART_TxData[1] = 0x03;
	UART_TxData[2] = 0x02;
	UART_TxData[3] = 0x00;
	UART_TxData[4] = 0x00;

	//add crc in reverse byte order
	uint16_t crc = UART_CRC(UART_TxData, 5);
	UART_TxData[5] = crc & 0xFF;
	UART_TxData[6] = crc >> 8;
	UART_TxData[7] = 0xFF; //add extra byte of zeros to match faraday protocol
	return 8;
}

/* Prep battery status 2 message (7 bytes). Refer to documentation for packet format
 * Fill UART_TxData to battery status message 2 - purpose unknown. Hard coded for now
 *
 * Example request 0x2 0x3 0x0 0x1 0x0 0x1 0xd5 0xf9
 * Example response 0x2 0x3 0x2 0x0 0x19 0x3d 0x8e
 */
uint8_t UART_PrepBatteryStatusMessage2() {

	//get highest cell temp

	for (int i = 0; i < 32; i++) {
		UART_TxData[i] = 0;
	}

	UART_TxData[0] = 0x02;
	UART_TxData[1] = 0x03;
	UART_TxData[2] = 0x02;
	UART_TxData[3] = 0x00;
	UART_TxData[4] = 0x19; //old hard coded value
	//UART_TxData[4] = batt.CellMaxT;

	//add crc in reverse byte order
	uint16_t crc = UART_CRC(UART_TxData, 5);
	UART_TxData[5] = crc & 0xFF;
	UART_TxData[6] = crc >> 8;

	UART_TxData[7] = 0xFF; //add extra byte of zeros to match faraday protocol
	return 8;
}

/*Takes in an 8 byte message, parses, checks CRC, and then responds with the appropriate message */
void UART_Respond(uint8_t *buf, uint16_t size) {

	//Code currently only supports 8 byte read messages, which is all that's necessary to get the bike moving.
	if (size == 8) {

		//unpack message
		uint8_t SlaveID = buf[0];
		uint8_t FunctionCode = buf[1];
		uint16_t Address = buf[2] << 8 | buf[3];
		uint16_t NumRegs = buf[4] << 8 | buf[5];
		uint16_t CRCRecv = buf[7] << 8 | buf[6];

		//Check CRC and that we're the target audience (BMS is 0x02)
		if (CRCRecv == UART_CRC(buf, 6) && SlaveID == 0x02) {
			delayUS(&htim2, 450); //insert 1ms delay to match timing of original battery
			if (FunctionCode == 0x03) { //it's a read
				if (LEDS) {
					HAL_GPIO_WritePin(LED_SF_PORT, LED_SF_PIN, GPIO_PIN_SET);
					delayUS(&htim2, 50);
					HAL_GPIO_WritePin(LED_SF_PORT, LED_SF_PIN, GPIO_PIN_RESET);
				}

				uint8_t len;

				if (Address == 0x02) { //Battery Voltage Message
					len = UART_PrepCellVoltageMessage();
					THVD2410_Transmit();
					HAL_UART_Transmit(&huart2, UART_TxData, len,
					UART_TIMEOUT_S);

				} else if (Address == 0x17) { //Battery Balancing Message
					len = UART_PrepCellBalancingMessage();
					THVD2410_Transmit();
					HAL_UART_Transmit(&huart2, UART_TxData, len,
					UART_TIMEOUT_S);

				} else if (Address == 0x00 && NumRegs == 0x01) { //Battery Status Message 1
					len = UART_PrepBatteryStatusMessage1();
					THVD2410_Transmit();
					HAL_UART_Transmit(&huart2, UART_TxData, len,
					UART_TIMEOUT_S);

				} else if (Address == 0x01 && NumRegs == 0x01) { //Battery Status Message 1
					len = UART_PrepBatteryStatusMessage2();
					THVD2410_Transmit();
					HAL_UART_Transmit(&huart2, UART_TxData, len,
					UART_TIMEOUT_S);
				}
			}
		}

	}
	THVD2410_Receive();
	HAL_GPIO_WritePin(LED_SF_PORT, LED_SF_PIN, GPIO_PIN_RESET);
}

/* State Machine Functions
 * ===================== */

/*Pet Independent Watchdog. Must be done once a second or sooner*/
void STM32_PetWatchdog() {

	/* Refresh IWDG: reload counter */
	if (HAL_IWDG_Refresh(&hiwdg) != HAL_OK) {
		/* Refresh Error */
		Error_Handler();
	}
}
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
int main(void) {

	/* MCU Configuration--------------------------------------------------------*/

	/* Reset of all peripherals, Initializes the Flash interface and the Systick. */

	HAL_Init();

	/* USER CODE BEGIN Init */
	if (!DEBUG) {
		STM32_CheckForWatchdogReset();
	}
	/* USER CODE END Init */

	/* Configure the system clock */
	SystemClock_Config();

	/* USER CODE BEGIN SysInit */
	MX_GPIO_Init();
	MX_ADC_Init();
	MX_I2C1_Init();
	MX_TIM2_Init();
	MX_USART2_UART_Init();
	SystemPower_Config();
	MX_RTC_Init();
	HAL_TIM_Base_Start(&htim2);
	/* USER CODE END SysInit */

	if (DEBUG) {
		printf("stm32 init complete\r\n");
	}

	/*Check to see if the button is currently pressed*/
	if (STM32_Wake_Button_Pressed()) {
		state.ButtonPressedDuringBoot = 1;
	}

	/* Check to see if the STOP flag is set from prior reset. If so, initiate STOP*/
	if (STM32_ShouldStop()) {
		if (DEBUG) {
			printf("stm32 reset with intent to sleep, time to sleep...zzz\r\n");
		}
		STM32_Stop();
	}

	/* Initialize BQ State*/
	BQ769x2_ResetShutdownPin(&batt); // RST_SHUT pin set low just in case
	BQ769x2_InitState(&batt, &hi2c1, BQ_DEV_ADDR, BQ_CRC_MODE, &htim2,
	ACTIVE_CELLS, RST_SHUT_PORT, RST_SHUT_PIN, CFETOFF_PORT, CFETOFF_PIN,
	DFETOFF_PORT, DFETOFF_PIN);

	delayMS(&htim2, 50); //Wait for everything to stabilize

	/* Init watchdog */
	if (WATCHDOG) {
		MX_IWDG_Init();
	}
	//BlinkForever(1); //uncomment to test IWDG

	/* Useful functions for debugging, especially if the STM32 gets into a weird state where it won't sleep */
	if (RESET_3V3) {
		HAL_GPIO_WritePin(LED_SF_PORT, LED_SF_PIN, GPIO_PIN_SET);
		BQ769x2_Reset(&batt); //Use this for several reasons - the main reason is to kill the 3.3V rail and power cycle the STM32, which may be necessary if the programmer puts it into a state where it won't sleep properly
	}

	UART_WaitForCommand(); //Start UART Receiving

	while (1) {

		/* USER CODE BEGIN 3 */
		BQ769x2_ForceDisableFETs(&batt); //disable FETs until we are getting communication from the BQ chip
		BQ769x2_SoftWake(&batt); //wiggle RST_SHUT to do a partial reset of the BQ chip. Not sure if this is necessary but it doesn't seem to hurt.

		if (DEBUG) {
			if (BQ769x2_ReadControlStatus(&batt) & 0x04) {
				printf("bq woke from DEEPSLEEP\r\n");
			}
		}

		//Check for BQ state FULLACCESS, SEALED, or UNSEALED. Device must be connected and ACKing to get past this point.
		// This may take quite a few reads for the chip to wake up if it's the first time it's booting (I've seen 15 reads!)
		while (!BQ769x2_Ready(&batt)) {
			if (DEBUG) {
				printf("bq not ready\r\n");
			}
			delayUS(&htim2, 1000);
			if (state.RetryCount > RETRY_LIMIT) {
				HAL_GPIO_WritePin(LED_SF_PORT, LED_SF_PIN, GPIO_PIN_SET);
				BQ769x2_Reset(&batt); //gotta reset the BQ and try again. This kills the 3V3 rail
			}
			state.RetryCount++;
		};

		state.RetryCount = 0;

		//Wake up the device if it isn't already awake
		while (!BQ769x2_Wake(&batt)) {
			if (DEBUG) {
				printf("bq not awake\r\n");
			}
			delayUS(&htim2, 1000);
			if (state.RetryCount > RETRY_LIMIT) {
				HAL_GPIO_WritePin(LED_SF_PORT, LED_SF_PIN, GPIO_PIN_SET);
				BQ769x2_Reset(&batt); //gotta reset the BQ and try again. This kills the 3V3 rail
			}
			state.RetryCount++;
		}

		state.RetryCount = 0;

		//Initialize registers by calling BQ769x2_Init and then checking that the configuration was successful
		// BQ769x2 does a spot check of a register that should have been configured if BQ769x2_Init() was successful.
		while (!BQ769x2_Initialize(&batt)) {
			if (DEBUG) {
				printf("bq not configured\r\n");
			}
			if (state.RetryCount > RETRY_LIMIT) {
				HAL_GPIO_WritePin(LED_SF_PORT, LED_SF_PIN, GPIO_PIN_SET);
				BQ769x2_Reset(&batt); //gotta reset the BQ and try again. This kills the 3V3 rail
			}
			state.RetryCount++;
		}

		state.RetryCount = 0;

		// get first ADC reading. Normal for this to take a few retries
		while (!BQ769x2_ReadBatteryData(&batt)) {
			if (state.RetryCount > RETRY_LIMIT) {
				HAL_GPIO_WritePin(LED_SF_PORT, LED_SF_PIN, GPIO_PIN_SET);
				BQ769x2_Reset(&batt); //gotta reset the BQ and try again. This kills the 3V3 rail
			}
			state.RetryCount++;
			delayUS(&htim2, 5000); //wait a bit for the ADC to finish measuring
		}

		state.RetryCount = 0;

		// check whether a charger >15V is connected and the button wasn't pressed during boot. If not, go back to sleep.
		if (!state.ButtonPressedDuringBoot && batt.Pack_Voltage < 15000) {
			if (DEBUG) {
				printf(
						"stm32 going back to sleep because user didn't press button and charger isn't connected...zzz\r\n");
			}
			Sleep();
		}

		//why are we starting? the only reasons are button press or charger detected
		if (DEBUG) {
			if (state.ButtonPressedDuringBoot) {
				printf("\r\nbutton pressed, time to attempt to allow FETs\r\n");
			}
			if (batt.Pack_Voltage > 15000) {
				printf("\r\ncharger connected, time to allow FETs\r\n");
			}
		}

		//Enable FETs because the BQ chip is up and running
		BQ769x2_AllowFETs(&batt);

		//Start UART interrupt
		UART_WaitForCommand();

		while (1) {

			//detect button press and take action if needed
			STM32_HandleButton();

			//Update FET registers and update LEDs
			BQ769x2_ReadFETStatus(&batt);
			if (LEDS) {
				STM32_UpdateFETLEDs();
			}

			//Handle sleep current and put battery to sleep if not much is going on
			STM32_HandleInactivity();

			//Useful for logging
			BQ769x2_CalcMinMaxCellV(&batt);

			//Needed for battery status message 2
			BQ769x2_CalcMinMaxCellT(&batt);

			//Print battery status over RS485 for debug
			BQ769x2_ReadBatteryStatus(&batt);
			if (DEBUG) {
				BQ769x2_PrintStatus(&batt);
			}

			//Get the latest data from the BQ chip
			if (BQ769x2_ReadBatteryData(&batt)) {
				state.RetryCount = 0;
			} else {
				state.RetryCount++;
			}

			//Check for faults and trigger the LED if so
			if (BQ769x2_ReadSafetyStatus(&batt)) {
				state.RetryCount = 0;
			} else {
				state.RetryCount++;
			};

			//Set Fault LED
			if (LEDS && (batt.ProtectionsTriggered & 1)) {
				HAL_GPIO_WritePin(LED_BF_PORT, LED_BF_PIN, GPIO_PIN_SET);
			} else {
				HAL_GPIO_WritePin(LED_BF_PORT, LED_BF_PIN, GPIO_PIN_RESET);
			}

			//If there are too many failures, reset the BQ chip
			if (state.RetryCount > RETRY_LIMIT) {
				HAL_GPIO_WritePin(LED_SF_PORT, LED_SF_PIN, GPIO_PIN_SET);
				if (!BQ769x2_Reset(&batt)) {
					Error_Handler(); //If we end up here, something is truly messed up
					//gotta reset the BQ and try again. This kills the 3V3 rail
				}
				break;
			}

			STM32_PetWatchdog();
			delayMS(&htim2, 10);  // repeat loop every 20 ms

		}
	}
	/* USER CODE END 3 */
}

PUTCHAR_PROTOTYPE {
	/* Place your implementation of fputc here */
	/* e.g. write a character to the EVAL_COM1 and Loop until the end of transmission */
	HAL_GPIO_WritePin(UART_RX_EN_PORT, UART_RX_EN_PIN, GPIO_PIN_SET); // Receive Off
	delayUS(&htim2, 20);
	HAL_GPIO_WritePin(UART_TX_EN_PORT, UART_TX_EN_PIN, GPIO_PIN_SET); // Transmit On
	delayUS(&htim2, 20);
	HAL_UART_Transmit(&huart2, (uint8_t*) &ch, 1, 0xFFFF);
	HAL_GPIO_WritePin(UART_TX_EN_PORT, UART_TX_EN_PIN, GPIO_PIN_RESET); //Transmit off
	delayUS(&htim2, 20);
	HAL_GPIO_WritePin(UART_RX_EN_PORT, UART_RX_EN_PIN, GPIO_PIN_SET); // Receive still off
	delayUS(&htim2, 20);

	return ch;
}

/**
 * @brief  Configures EXTI Port A PIN 0 as an interrupt
 * @param  None
 * @retval None
 */
static void EXTI0_1_IRQHandler_Config(void) {
	GPIO_InitTypeDef GPIO_InitStructure;

	/* Enable GPIOC clock */
	__HAL_RCC_GPIOA_CLK_ENABLE();

	/* Configure PC.13 pin as input floating */
	GPIO_InitStructure.Mode = GPIO_MODE_IT_FALLING;
	GPIO_InitStructure.Pull = GPIO_PULLUP;
	GPIO_InitStructure.Pin = GPIO_PIN_0;
	HAL_GPIO_Init(GPIOA, &GPIO_InitStructure);

	/* Enable and set EXTI lines 4 to 15 Interrupt to the lowest priority */
	HAL_NVIC_SetPriority(EXTI0_1_IRQn, 2, 0);
	HAL_NVIC_EnableIRQ(EXTI0_1_IRQn);
}

/**
 * @brief  Configures EXTI Port B Pin 5 as an interrupt
 * @param  None
 * @retval None
 */
static void EXTI2_3_IRQHandler_Config(void) {
	GPIO_InitTypeDef GPIO_InitStructure;

	/* Enable GPIOC clock */
	__HAL_RCC_GPIOB_CLK_ENABLE();

	/* Configure PC.13 pin as input floating */
	GPIO_InitStructure.Mode = GPIO_MODE_IT_RISING;
	GPIO_InitStructure.Pull = GPIO_PULLDOWN;
	GPIO_InitStructure.Pin = GPIO_PIN_5;
	HAL_GPIO_Init(GPIOB, &GPIO_InitStructure);

	/* Enable and set EXTI lines 4 to 15 Interrupt to the lowest priority */
	HAL_NVIC_SetPriority(EXTI2_3_IRQn, 2, 0);
	HAL_NVIC_EnableIRQ(EXTI2_3_IRQn);
}

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
/* USER CODE BEGIN 4 */
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

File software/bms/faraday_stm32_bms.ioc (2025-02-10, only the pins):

Mcu.UserName=STM32L010K8Tx
PA0.Signal=SYS_WKUP1
PA1.Signal=GPIO_Output
PA13.Signal=SYS_SWDIO
PA14.Signal=SYS_SWCLK
PA2.Signal=USART2_TX
PA3.Signal=USART2_RX
PA5.Signal=SharedAnalog_PA5
PA8.Signal=GPIO_Output
PA9.Signal=GPIO_Output
PB0.Signal=GPIO_Output
PB1.Signal=GPIO_Output
PB3.Signal=GPIO_Output
PB4.Signal=GPIO_Output
PB5.Signal=GPIO_Input
PB6.Signal=I2C1_SCL
PB7.Signal=I2C1_SDA
PC14-OSC32_IN.Signal=RCC_OSC32_IN
PC15-OSC32_OUT.Signal=RCC_OSC32_OUT

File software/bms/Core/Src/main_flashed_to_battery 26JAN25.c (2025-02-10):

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
/* Includes ------------------------------------------------------------------*/
#include "main.h"
#include "BQ769x2Header.h"
#include "stdio.h"

ADC_HandleTypeDef hadc;

I2C_HandleTypeDef hi2c1;

TIM_HandleTypeDef htim2;

UART_HandleTypeDef huart2;

IWDG_HandleTypeDef hiwdg;

RTC_HandleTypeDef hrtc;

/* Code Modes */
#define DEBUG 0 //Debug mode disables RS485 communications to the bike and instead enables debug messages over RS485, including printf
#define LEDS 0 //Set to 1 to enable LEDs, 0 to disable. LEDs consume surprisingly large amounts of power because of the linear regulator from 48V to 3.3V

/*BQ Parameters */
#define DEV_ADDR  0x10  // BQ769x2 address is 0x10 including R/W bit or 0x8 as 7-bit address
#define CRC_Mode 1  // 0 for disabled, 1 for enabled

/*Pin Definitions
 * --------------
 * Note - I2C Pin definitions and RS485 TX/RX definitions are handled in HAL init functions*/

//LED that indicates CHG state
#define LED_CHG_PORT GPIOB
#define LED_CHG_PIN GPIO_PIN_0

//LED that indicates DSG state
#define LED_DSG_PORT GPIOB
#define LED_DSG_PIN GPIO_PIN_1

//Active-high to veto charge FET
#define CFETOFF_PORT GPIOB
#define CFETOFF_PIN GPIO_PIN_3

//Active-high to veto discharge FET
#define DFETOFF_PORT GPIOB
#define DFETOFF_PIN GPIO_PIN_4

//Active-low on-button from faraday bike. Used in this file and stm32l0xx_it.c
#define BUTTON_PORT GPIOA
#define BUTTON_PIN GPIO_PIN_0

//RST_SHUT_CTRL used by STM to change BQ sleep states
#define RST_SHUT_CTRL_PORT GPIOA
#define RST_SHUT_CTRL_PIN GPIO_PIN_1

//REG18 analog value from BQ chip. Read to check if BQ is in SHUTDOWN
#define REG18_AIN_PORT GPIOA
#define REG18_AIN_PIN GPIO_PIN_5

//LED2 General Purpose
#define LED_BF_PORT GPIOA
#define LED_BF_PIN GPIO_PIN_8

//LED3 General Purpose
#define LED_SF_PORT GPIOA
#define LED_SF_PIN GPIO_PIN_9

//Alert configurable output from BQ chip. Not used in this file, set in stm32l0xx_it.c
#define ALERT_PORT GPIOB
#define ALERT_PIN GPIO_PIN_5

//UART_TX_EN - enable transmit on RS485 transceiver, active high
#define UART_TX_EN_PORT GPIOA
#define UART_TX_EN_PIN GPIO_PIN_6

//UART_RX_EN - enable receive on RS485 transceiver, active low
#define UART_RX_EN_PORT GPIOA
#define UART_RX_EN_PIN GPIO_PIN_7

/* User-Facing Timing Parameters */
#define RETRY_LIMIT 100 //number of times the STM will retry communications with BQ before calling for a hard reset
#define INACTIVITY_LOOPS_MAX 15000 //number of loops without significant battery current before bike goes into sleep. Normally around 5 minutes for 10,000 loops
#define BUTTON_LONG_PRESS_LOOPS 15 //number of loops that count as a long press
#define UART_TIMEOUT_S 3 //default timeout for RS485 in seconds
#define PACK_CURRENT_INACTIVITY_LOWER_LIMIT_MA -250
#define PACK_CURRENT_INACTIVITY_UPPER_LIMIT_MA 75

/* Fake Enums */
#define R 0 // Read; Used in BQ769x2_DirectCommand and Subcommands functions
#define W 1 // Write; Used in BQ769x2_DirectCommand and Subcommands functions
#define W2 2 // Write data with two bytes; Used in Subcommands function

/*Uart Variables flag*/
__IO ITStatus UartBusy = RESET;

/* USER CODE BEGIN PV */
#define MAX_BUFFER_SIZE 32
uint8_t RX_1Byte[1] = { 0x00 };
uint8_t RX_data[2] = { 0x00, 0x00 }; // used in several functions to store data read from BQ769x2
uint8_t RX_4Byte[4] = { 0x00, 0x00, 0x00, 0x00 };
uint8_t RX_32Byte[32] = { 0x00, 0x00, 0x00, 0x00, 0x00, 0x00, 0x00, 0x00, 0x00,
		0x00, 0x00, 0x00, 0x00, 0x00, 0x00, 0x00, 0x00, 0x00, 0x00, 0x00, 0x00,
		0x00, 0x00, 0x00, 0x00, 0x00, 0x00, 0x00, 0x00, 0x00, 0x00, 0x00 };

// Global Variables for cell voltages, temperatures, Stack voltage, PACK Pin voltage, LD Pin voltage, CC2 current
int16_t CellVoltage[16] = { 0x00, 0x00, 0x00, 0x00, 0x00, 0x00, 0x00, 0x00,
		0x00, 0x00, 0x00, 0x00, 0x00, 0x00, 0x00, 0x00 };
int16_t CellMinV = 0;
int16_t CellMaxV = 0;
float Temperature[4] = { 0, 0, 0, 0 };
int8_t Offset[4] = { 0, 0, 0, 0 };
uint16_t Stack_Voltage = 0x00;
uint16_t Pack_Voltage = 0x00;
uint16_t LD_Voltage = 0x00;
int16_t Pack_Current = 0x00;
uint16_t test_var = 0x00;
uint16_t AlarmBits = 0x00;
uint8_t value_SafetyStatusA;  // Safety Status Register A
uint8_t value_SafetyStatusB;  // Safety Status Register B
uint8_t value_SafetyStatusC;  // Safety Status Register C
uint8_t value_PFStatusA;   // Permanent Fail Status Register A
uint8_t value_PFStatusB;   // Permanent Fail Status Register B
uint8_t value_PFStatusC;   // Permanent Fail Status Register C
uint16_t value_BatteryStatus; //battery status a
uint8_t FET_Status;  // FET Status register contents  - Shows states of FETs
uint16_t CB_ActiveCells;  // Cell Balancing Active Cells
uint8_t UV_Fault = 0;   // under-voltage fault state
uint8_t OV_Fault = 0;   // over-voltage fault state
uint8_t SCD_Fault = 0;  // short-circuit fault state
uint8_t OCD_Fault = 0;  // over-current fault state
uint8_t ProtectionsTriggered = 0; // Set to 1 if any protection triggers
uint8_t LD_ON = 0;	// Load Detect status bit
uint8_t DSG = 0;   // discharge FET state
uint8_t CHG = 0;   // charge FET state
uint8_t PCHG = 0;  // pre-charge FET state
uint8_t PDSG = 0;  // pre-discharge FET state

uint32_t AccumulatedCharge_Int; // in BQ769x2_READPASSQ func
uint32_t AccumulatedCharge_Frac; // in BQ769x2_READPASSQ func
uint32_t AccumulatedCharge_Time; // in BQ769x2_READPASSQ func

//Used for state machine
uint8_t BUTTON_COUNT = 0;
uint16_t CRC_FAIL = 0;
uint16_t INACTIVITY_COUNT = 0;
uint16_t RETRY_COUNT = 0;
uint8_t RESET_BY_WATCHDOG = 0;
uint8_t BUTTON_PRESSED_DURING_BOOT = 0;

//Used by UART
uint8_t UART_RxData[8] = { 0x00, 0x00, 0x00, 0x00, 0x00, 0x00, 0x00, 0x00 };
uint8_t UART_TxData[32] = { 0x00, 0x00, 0x00, 0x00, 0x00, 0x00, 0x00, 0x00,
		0x00, 0x00, 0x00, 0x00, 0x00, 0x00, 0x00, 0x00, 0x00, 0x00, 0x00, 0x00,
		0x00, 0x00, 0x00, 0x00, 0x00, 0x00, 0x00, 0x00, 0x00, 0x00, 0x00, 0x00 };

/* USER CODE END PV */

void SystemClock_Config(void);
static void SystemPower_Config(void);
static void MX_GPIO_Init(void);
static void MX_ADC_Init(void);
static void MX_I2C1_Init(void);
static void MX_USART2_UART_Init(void);
static void MX_TIM2_Init(void);
static void MX_IWDG_Init(void);
static void MX_RTC_Init(void);
static void EXTI0_1_IRQHandler_Config(void);
static void EXTI2_3_IRQHandler_Config(void);
static void THVD2410_Sleep();
static void THVD2410_Transmit();
static void THVD2410_Receive();
static uint8_t UART_PrepCellVoltageMessage();
static uint8_t UART_PrepCellBalancingMessage();
static uint8_t UART_PrepBatteryStatusMessage1();
static uint8_t UART_PrepBatteryStatusMessage2();
uint8_t STM32_Wake_Button_Pressed();
uint16_t BQ769x2_ReadControlStatus();
void Sleep();

#ifdef __GNUC__
/* With GCC, small printf (option LD Linker->Libraries->Small printf
 set to 'Yes') calls __io_putchar() */
#define PUTCHAR_PROTOTYPE int __io_putchar(int ch)
#else
#define PUTCHAR_PROTOTYPE int fputc(int ch, FILE *f)
#endif /* __GNUC__ */

/**
 * @brief  Retargets the C library printf function to the USART.
 * @param  None
 * @retval None
 */
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

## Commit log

2025-02-10 Initial upload
    Initial upload of V2 of battery mechanical, schematic, layout, and software.
    [5104.step, BOM-FakePack.csv, BOM-pcb_battery.csv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]
2025-02-13 Added battery RS485 messages to readme
2025-02-22 Added mechanical files and updated BOM for build.
    [end_bracket_non_wire_side-v10.step, end_bracket_non_wire_side-v10.stl, end_bracket_wire_side-v31.step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]
2025-02-23 Added Permanent Fail protections for Safety Undervoltage and Safety Overvoltage
    [main.c]
2025-02-26 Undervoltage lock-out and spinning LED fix
    Changes:
    - Implemented use of the Permanent Fail feature of the BQ76972 to prevent charge permanently if a cell drops below 1.9V or rises above 4.5V.
    - Implemented use of the Permanent Fail feature of the BQ76972 to compare the measured stack voltage versus the sum of cell voltages to detect missing cells or bad ADCs.
    - Reduced the top-of-charge turn-off time from 5 minutes or so to <2 seconds to try and resolve the spinning LED issue.
    [main.c]
2025-02-27 Fixed and verified spinning LED issue
    Just need to turn off the battery a bit more quickly than 5 minutes at end of charge. A few seconds seems to work.
    [main.c]
2025-02-27 Reduced idle timeout to match headlight timeout
    LED headlight was turning off a few minutes before the idle timeout on the battery. Reduced the timeout by 36%.
2025-02-27 Added .hex and .bin file generation to STM32 project
2025-02-28 Added Release config to STM32CubeIDE Project
2025-03-06 Removed unnecessary files from kicad output
2025-03-17 Down to 14 errors
    [BQ769x2.c, main.c]
2025-03-19 changed battery status 2 to include cell max temp. Untested.
2025-03-19 updates to i2C code - needs testing
    removed last reference to i2c_readreg in favor of the one that doesn't segfault. Need to test this to verify.
    [BQ769x2.c]
2025-03-24 BQ-refactor flashed onto battery
    Seems to be working. Had some issues that haven't been explained with my test PCB.
    [BQ769x2.c, main.c]
2025-03-26 Adjusted OV threshold down by 50mV
    Expect to top out at 4.1V instead of 4.15 for longer life while plugged in. Hope to roughly halve the degradation if left plugged in over winter.
    Also added some instructions and comments to BQ769x2.h
2025-03-30 Rotated diodes to fix only hardware issue.
    D19 and D22 were flipped on the schematic and this propagated to the PCB. All boards from round 2 needed to be reworked to rotate D19 and D22 180deg.
    [faraday-rescue-bms.kicad_pcb, faraday_STM32.kicad_sch]
2025-06-18 Fixed https://github.com/nhallsny/faraday-rescue/issues/7
    Fix for https://github.com/nhallsny/faraday-rescue/issues/7 changing data payload of battery status 2 back to hardcoded value. Seemed to fix the issue on the one bike that showed this problem.
    [main.c]
2025-07-01 PCB update
    Updated Gerber output files to include TVS diode fix
    [BOM-faraday-rescue-bms.csv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]
2025-07-01 Removed lonely gerber files, preferring .zip
    [pcb_battery_stub-CuBottom.gbr, pcb_battery_stub-CuIn1.gbr, pcb_battery_stub-CuIn2.gbr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]
2025-07-01 Replaced with older, more complete version of BOM and CPL
    [BOM-faraday-rescue-bms.csv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]
2025-11-17 Update README.md with updated part numbers and link to carbon fiber tube
2025-11-17 Update README.md with link to 15mm breather patches used in build
2026-03-29 Add mode-selector-less c option
    Added main_hardcode_mode_selector_highspeed29MAR2026.c to force the bike into the high torque mode if the mode selector is missing or broken. Compile with this file instead of main.c to ask the battery to respond to the mode selector message with 'I'm in high torque mode"
    [main_hardcode_mode_selector_high_speed29MAR2026.c]
2026-04-05 Update BOM-faraday-rescue-bms.csv
    Replaced D19,D21 with bidirectional to avoid confusion with silkscreen
    Replace BAT54SW with JLCPCB in stock variant
    [BOM-faraday-rescue-bms.csv]
2026-04-06 Update BOM-faraday-rescue-bms.csv
    Fix error in component sizing for R45,R36, C35,C36
    [BOM-faraday-rescue-bms.csv]

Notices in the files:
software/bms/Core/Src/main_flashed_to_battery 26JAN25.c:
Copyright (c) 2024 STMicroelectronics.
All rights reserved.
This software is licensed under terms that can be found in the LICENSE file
